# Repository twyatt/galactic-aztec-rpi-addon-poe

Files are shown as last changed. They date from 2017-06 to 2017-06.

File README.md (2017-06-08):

# About
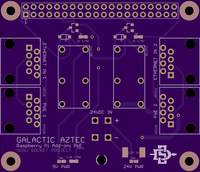
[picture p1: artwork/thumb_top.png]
OSHPark PCB Top Thumbnail

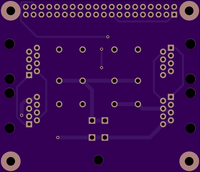
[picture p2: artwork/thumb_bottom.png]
OSHPark PCB Bottom Thumbnail


Custom Raspberry Pi Add-on board used as a PoE (power over ethernet) switch for the [Galactic Aztec] rocket. The board has a single Mini Fit Jr. port for PoE power input and 2 pairs of passthru ethernet ports that can have the PoE power toggled on/off.

Custom EagleCAD parts on this board can be found in the [SDSU Rocket Eagle Libraries].

## Wiring
The ethernet ports adhere to the following [10/100 mode B, DC on spares] wiring configuration:

| Pin | T568B Color  | Function |
|:---:|:---:|:---:|
| 1 | Orange/White | Rx + |
| 2 | Orange | Rx - |
| 3 | Green/White  | Tx + |
| 4 | Blue | DC + |
| 5 | Blue/White | DC + |
| 6 | Green | Tx - |
| 7 | Brown/White  | DC - |
| 8 | Brown | DC - |

## Launch
For the [Galactic Aztec April 18th, 2015 launch], this board was used in conjunction with the [Galactic Aztec Raspberry Pi Add-on: Power] board to allow the rocket to be powered by external power provided by the ground station (conserving onboard battery power). Then during pre-launch sequence the PoE power was toggled off, thereby having the rocket use onboard battery power.

# Bill of Materials
| Qty | Name | Description | Part Number | Vendor |
|:---:|:---:|---|---:|---|
| 2 | RELAY[1,2] | Relay 5V 5A DPST-NC (2 Form B) | [Z3640-ND] | DigiKey  |
| 2 | Q1, Q2 | Transistor NPN 40V 600mA SOT-23-3 | [MMBT2222ATPMSCT-ND] | DigiKey  |
| 2 | R1, R2 | Resistor 1k 1/4W 1% 0603 | [RHM1.00KADCT-ND] | DigiKey  |
| 2 | D1, D2 | Diode 50V 1A SOD-123 | [SM4001PL-TPMSCT-ND] | DigiKey  |
| 4 | RJ45-[1-4] | Jack RJ45 CAT5/CAT5e | [380-1046-ND] | DigiKey  |
| 1 | | Molex Mini Fit Jr. 4-pos Right Angle | [WM1352-ND] | DigiKey  |
| 2 | D3, D4 | LED Red Vf=1.8V If=2mA 0603 | [475-1195-2-ND] | DigiKey  |
| 1 | R4 | Resistor 1.8kΩ 1/4W 1% 0603 | [P1.8KBYCT-ND] | DigiKey  |
| 1 | R3 | Resistor 12kΩ 1/4W 1% 0603 | [RHM12.0KADCT-ND] | DigiKey  |
| 1 | | Header Stacking 2x20 Tall 23mm | [1979] | Adafruit |

[Galactic Aztec]: http://rocket.sdsu.edu/rockets
[SDSU Rocket Eagle Libraries]: https://github.com/twyatt/SDSURocket-Eagle-Libraries
[10/100 mode B, DC on spares]: https://en.wikipedia.org/wiki/Power_over_Ethernet#Pinouts
[Galactic Aztec April 18th, 2015 launch]: https://github.com/twyatt/galactic-aztec-launch-data
[Galactic Aztec Raspberry Pi Add-on: Power]: https://github.com/twyatt/galactic-aztec-rpi-addon-power
[Z3640-ND]: http://www.digikey.com/product-detail/en/G6B-2014P-US%20DC5/Z3640-ND/1815886
[MMBT2222ATPMSCT-ND]: http://www.digikey.com/product-detail/en/MMBT2222A-TP/MMBT2222ATPMSCT-ND/717394
[RHM1.00KADCT-ND]: http://www.digikey.com/product-detail/en/ESR03EZPF1001/RHM1.00KADCT-ND/1983752
[SM4001PL-TPMSCT-ND]: http://www.digikey.com/product-detail/en/SM4001PL-TP/SM4001PL-TPMSCT-ND/1793403
[380-1046-ND]: http://www.digikey.com/product-detail/en/SS-7188-NF/380-1046-ND/388308
[WM1352-ND]: http://www.digikey.com/product-search/en?x=0&y=0&lang=en&site=us&keywords=538-39-30-1040
[475-1195-2-ND]: http://www.digikey.com/product-detail/en/LS%20L29K-H1J2-1-Z/475-1195-1-ND/810356
[P1.8KBYCT-ND]: http://www.digikey.com/product-detail/en/ERJ-PA3F1801V/P1.8KBYCT-ND/5036145
[RHM12.0KADCT-ND]: http://www.digikey.com/product-detail/en/ESR03EZPF1202/RHM12.0KADCT-ND/1983756
[1979]: https://www.adafruit.com/product/1979

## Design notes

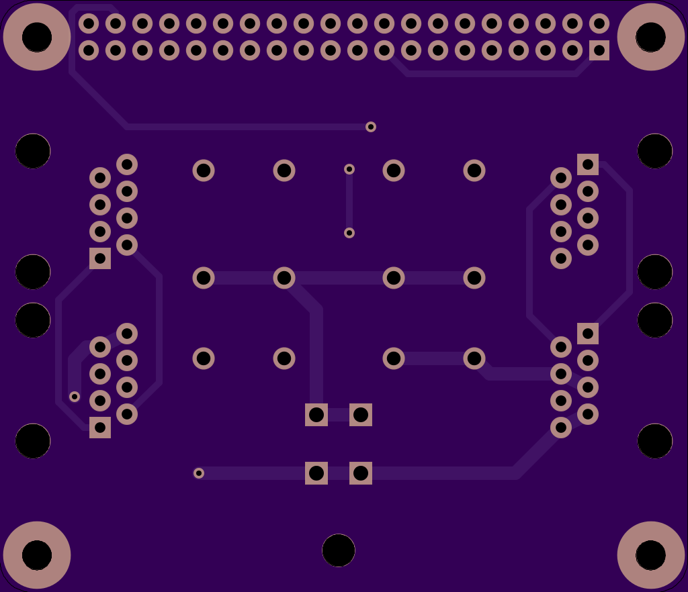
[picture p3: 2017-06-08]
artwork/bottom.png

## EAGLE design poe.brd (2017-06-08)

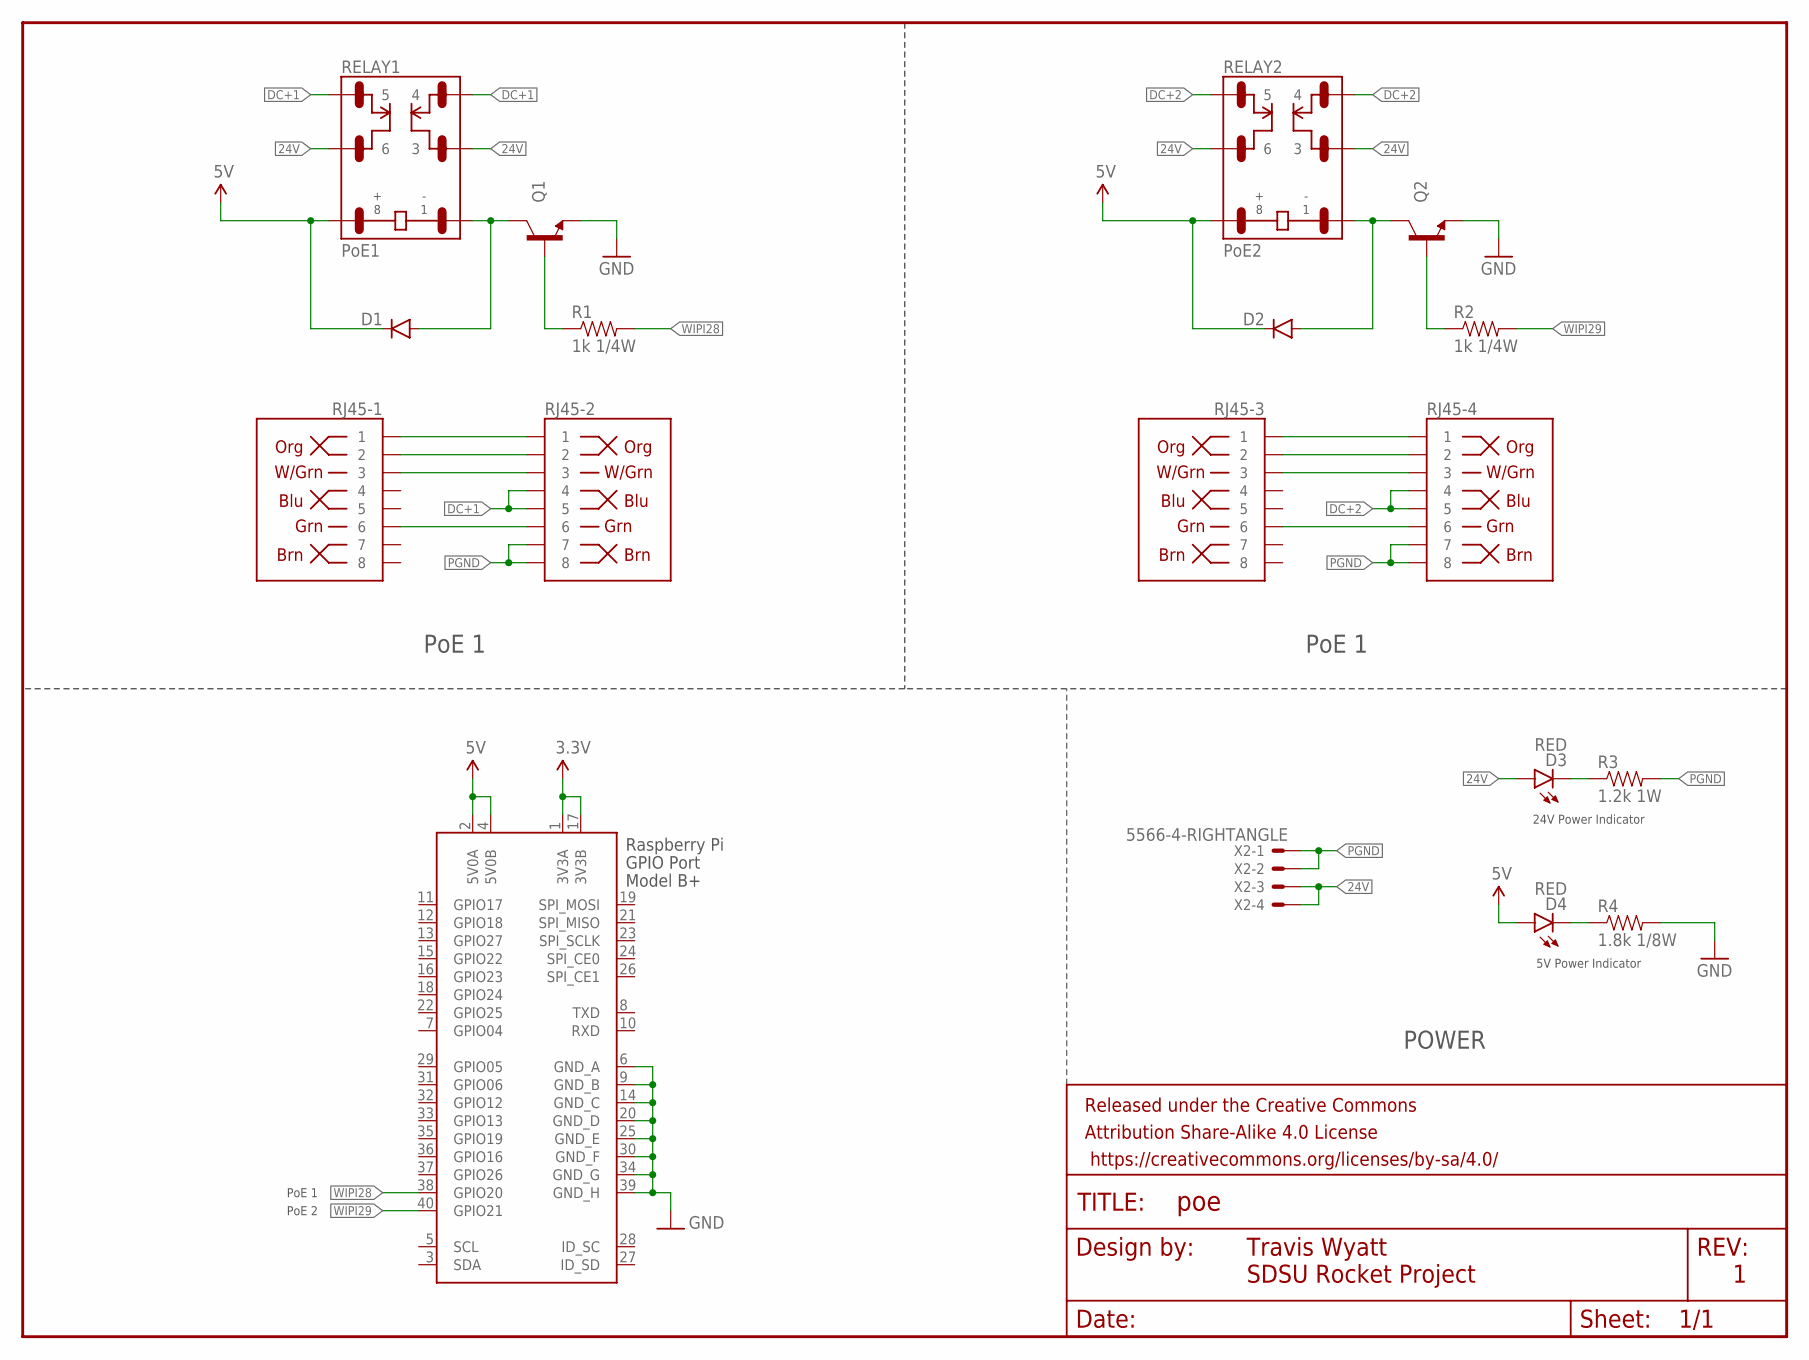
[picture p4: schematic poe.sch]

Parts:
D1, D2: DIODESOD123; SOD-123
D3, D4: RED; LED-0603
FRAME1: FRAME-LETTER; CREATIVE_COMMONS
Q1, Q2: TRANSISTOR_NPNSOT23-3; SOT23-3
R1, R2: 1k 1/4W; 0603-RES
R3: 1.2k 1W; R2512
R4: 1.8k 1/8W; 0603-RES
RELAY1: PoE1; G6B-2
RELAY2: PoE2; G6B-2
RJ45-1, RJ45-2, RJ45-3, RJ45-4: RJ45-8PTH; RJ45-8
X1: RASPI_BOARD_B+#_H; RASPI_BOARD_B+HAT
X2: 5566-4-RIGHTANGLE; 5566-4

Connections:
3.3V: X1.1 (3V3A), X1.17 (3V3B)
5V: D1.C, D2.C, D4.A, RELAY1.8, RELAY2.8, X1.2 (5V0A), X1.4 (5V0B)
24V: D3.A, RELAY1.3, RELAY1.6, RELAY2.3, RELAY2.6, X2.3, X2.4
DC+1: RELAY1.4, RELAY1.5, RJ45-2.4, RJ45-2.5
DC+2: RELAY2.4, RELAY2.5, RJ45-4.4, RJ45-4.5
GND: Q1.2 (E), Q2.2 (E), R4.2, X1.6 (GND_A), X1.9 (GND_B), X1.14 (GND_C), X1.20 (GND_D), X1.25 (GND_E), X1.30 (GND_F), X1.34 (GND_G), X1.39 (GND_H)
unnamed: Q1.1 (B), R1.1
unnamed: D1.A, Q1.3 (C), RELAY1.1
unnamed: D3.C, R3.1
unnamed: D4.C, R4.1
unnamed: D2.A, Q2.3 (C), RELAY2.1
unnamed: Q2.1 (B), R2.1
unnamed: RJ45-1.1, RJ45-2.1
unnamed: RJ45-1.2, RJ45-2.2
unnamed: RJ45-1.3, RJ45-2.3
unnamed: RJ45-1.6, RJ45-2.6
unnamed: RJ45-3.1, RJ45-4.1
unnamed: RJ45-3.2, RJ45-4.2
unnamed: RJ45-3.3, RJ45-4.3
unnamed: RJ45-3.6, RJ45-4.6
PGND: R3.2, RJ45-2.7, RJ45-2.8, RJ45-4.7, RJ45-4.8, X2.1, X2.2
WIPI28: R1.2, X1.38 (GPIO20)
WIPI29: R2.2, X1.40 (GPIO21)

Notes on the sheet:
PoE 1
POWER
Travis Wyatt
SDSU Rocket Project
24V Power Indicator
5V Power Indicator
PoE 2

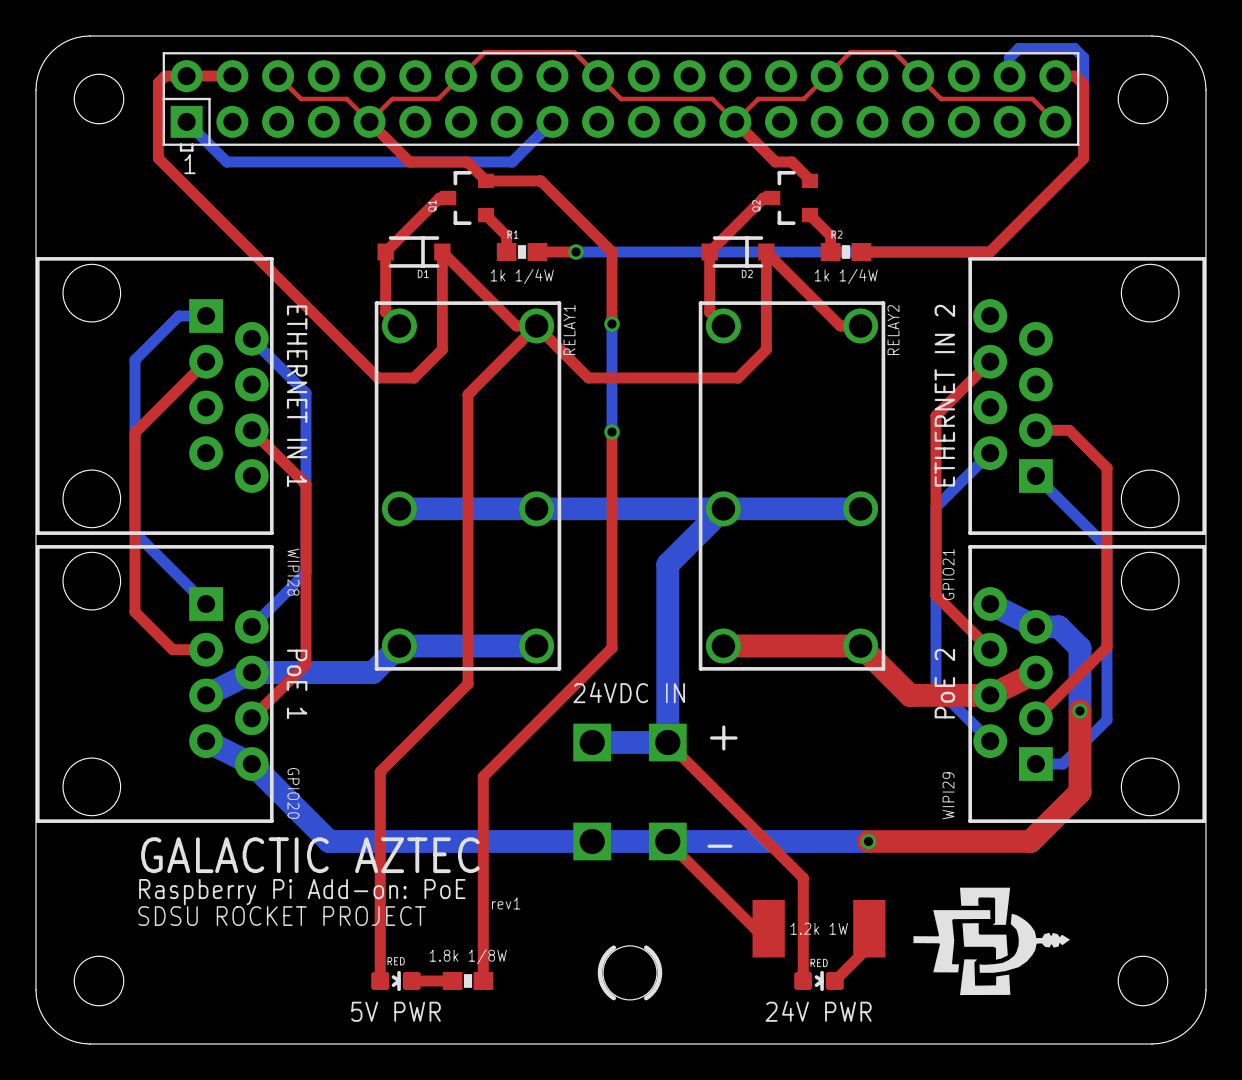
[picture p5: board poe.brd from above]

Board: 2 copper layers, 65.0 x 56.0 mm, 19 parts (0 on the bottom side), 23 nets.

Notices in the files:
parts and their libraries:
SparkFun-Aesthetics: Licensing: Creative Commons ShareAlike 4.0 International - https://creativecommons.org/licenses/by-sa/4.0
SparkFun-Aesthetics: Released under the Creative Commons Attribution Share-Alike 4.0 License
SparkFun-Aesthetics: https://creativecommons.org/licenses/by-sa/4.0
